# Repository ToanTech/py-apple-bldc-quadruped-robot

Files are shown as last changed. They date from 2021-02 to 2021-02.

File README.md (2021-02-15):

# py-apple-bldc-quadruped-robot
# 菠萝无刷四足机器人项目

## 1 简介  

  菠萝无刷四足机器人项目是由灯哥开源的，属于菠萝四足机器人项目的无刷分支。目前开源的机器人为  **菠萝无刷1代 测试版**。

  相应的文档和说明仍在不断撰写完善中，目前本 Github 的文件开源的内容主要为 **菠萝无刷1代 测试版** 的所有机械结构和软件程序；而机器人所采用的无刷电机FOC驱动开源资料和搭建方法开源在了另外的 Github上，见：  [灯哥开源FOC双路迷你无刷电机驱动](https://github.com/ToanTech/Deng-s-foc-controller)

  [菠萝无刷四足机器人项目总链接入口](https://github.com/ToanTech/py-apple-quadruped-robot)

## 2 项目文件说明

* src文件夹：存放测试本无刷四足机器人的 Pyboard 主控代码
* 3D model 文件夹：存放 菠萝无刷一代 三维模型
* BOM 文件夹：存放 菠萝无刷一代  机械+电控 BOM 表

## 3  项目原理及搭建教程

   本项目原理及搭建教程请见B站教学视频：

 [【教程】成本1K！从0教你DIY无刷四足机器人~灯哥无刷四足一代实验版开源啦！！！](https://www.bilibili.com/video/BV1kV411i76z/)

  DIY过程中由任何问题，欢迎加入QQ群聊交流：

  **开源无刷四足机器人交流群：1005923565**

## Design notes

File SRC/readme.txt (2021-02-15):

使用说明

1. Pyboard 测试程序放在基于 STM32 F4 的 Pyboard 内存之中
2. 灯哥开源FOC无刷驱动 程序 烧录进 灯哥开源无刷驱动版的 ESP32主控之中

前期文档未完善阶段，有问题欢迎加QQ群咨询：1005923565

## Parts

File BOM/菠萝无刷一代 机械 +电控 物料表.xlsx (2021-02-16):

部分名称 | 物料名称 | 物料规格 | 数量 | 注意
机械-单腿 | 螺丝 | M3*10 | 20 | 此为单腿数量，四条腿数量需x4
机械-单腿 | 螺丝 | M3*15 | 20 | 此为单腿数量，四条腿数量需x5
机械-单腿 | 螺丝 | M3*20 | 20 | 此为单腿数量，四条腿数量需x6
机械-单腿 | 轴承 | 6701ZZ | 2 | 此为单腿数量，四条腿数量需x7
机械-单腿 | 轴承 | 6704ZZ | 2 | 此为单腿数量，四条腿数量需x8
机械-单腿 | 防松螺母 | M3 | 10 | 此为单腿数量，四条腿数量需x9
机械-单腿 | 自行车车轮胶皮（足底防滑） | 根据实际需要 | 根据实际需要 | 此为单腿数量，四条腿数量需x10
机械-单腿 | 云台无刷电机 | 4008 150T（或类似参数电机） | 2 | 此为单腿数量，四条腿数量需x11
机械-单腿 | 同步带 | HTD-3M 318 6MM | 2 | 此为单腿数量，四条腿数量需x12
机械-身体 | 螺丝 | 3M*35 | 16
电控 | 电池 | 4S 16.8V电池 | 1
电控 | PyBoard | 基于STM32F4 的Pyboard | 1
电控 | 灯哥开源FOC无刷驱动板 | 见灯哥开源无刷驱动器GitHUB | 4
电控 | 杜邦线 |  | 若干

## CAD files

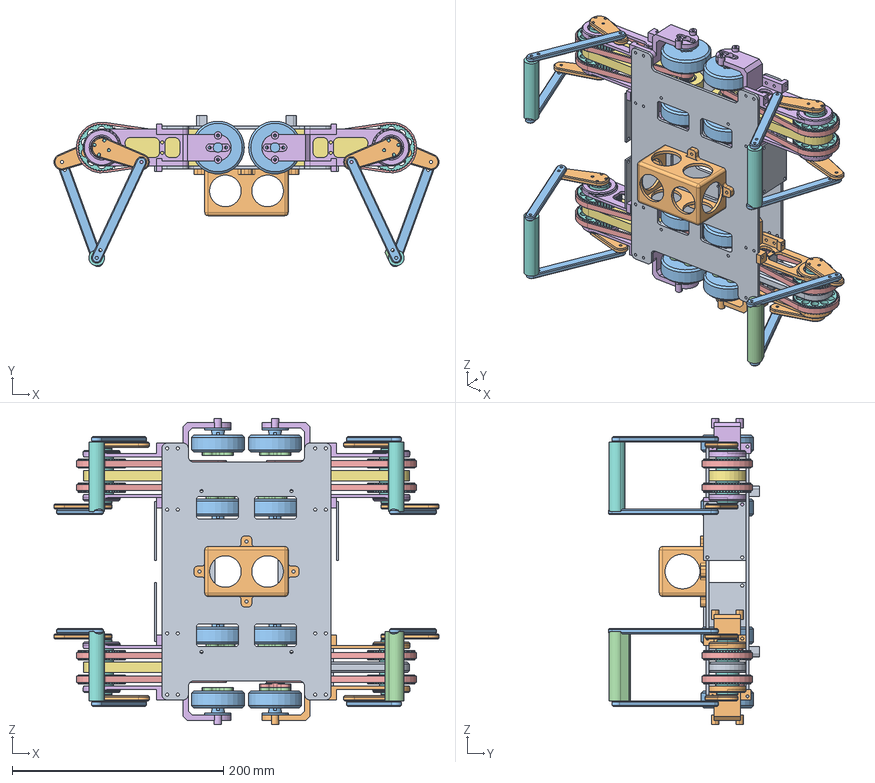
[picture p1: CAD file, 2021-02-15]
3D model/Py-apple BLDC quadruped robot V1.0.stp
364.1 x 143.2 x 289.8 mm
BODY_BOARD_V2 x 2
MOTOR_BINDER_V2 x 2
4008-MOTOR x 2
PULLEY_BRACKET x 2
REV_2_SMALL_PULLEY_LONG_PRINT x 2
OUTER_BEARING_6704-ZZ x 4
INNER_BEARING_6701-ZZ x 2
SDP_A_6A53M048NF0908_1 x 2
BACKGAP
TEST_N_GAN1 x 2
TEST_N_GAN_6 x 2
FOOT_FOOT
HTD210_3M_V2 x 2
MOTOR_BINDER_V2_MIR x 4
4008-MOTOR_MIR x 4
PULLEY_BRACKET_MIR x 4
OUTER_BEARING_6704-ZZ_MIR x 8
INNER_BEARING_6701-ZZ_MIR x 4
SDP_A_6A53M048NF0908_1_MIR x 4
BACKGAP_MIR x 2
TEST_N_GAN1_MIR x 4
TEST_N_GAN_6_MIR x 4
FOOT_FOOT_MIR x 2
HTD210_3M_V2_MIR x 4
BLDC_PCB_MIR x 2
MOTOR_BINDER_V2_MIR_MIR x 2
4008-MOTOR_MIR_MIR x 2
PULLEY_BRACKET_MIR_MIR x 2
OUTER_BEARING_6704-ZZ_MIR_MIR x 4
INNER_BEARING_6701-ZZ_MIR_MIR x 2
SDP_A_6A53M048NF0908_1_MIR_MIR x 2
BACKGAP_MIR_MIR
TEST_N_GAN1_MIR_MIR x 2
TEST_N_GAN_6_MIR_MIR x 2
FOOT_FOOT_MIR_MIR
HTD210_3M_V2_MIR_MIR x 2
BLDC_PCB_MIR_MIR
BATTERY_BIND_GAP

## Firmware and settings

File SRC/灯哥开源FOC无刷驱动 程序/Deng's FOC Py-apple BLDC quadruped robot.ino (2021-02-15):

/**
Copyright Deng（灯哥） (ream_d@yeah.net)  Py-apple dog project
Github:https:#github.com/ToanTech/py-apple-quadruped-robot
Licensed under the Apache License, Version 2.0 (the "License")
you may not use this file except in compliance with the License.
You may obtain a copy of the License at:http:#www.apache.org/licenses/LICENSE-2.0
 */
#include <SimpleFOC.h>
double init_p_sensor=0;
double init_p_sensor1=0;
int commaPosition;                //存储还没有分离出来的字符串 
double motor1_angle,motor2_angle;

MagneticSensorI2C sensor = MagneticSensorI2C(AS5600_I2C);
MagneticSensorI2C sensor1 = MagneticSensorI2C(AS5600_I2C);
TwoWire I2Cone = TwoWire(0);
TwoWire I2Ctwo = TwoWire(1);

// Motor instance
BLDCMotor motor = BLDCMotor(7);
BLDCDriver3PWM driver = BLDCDriver3PWM(32, 33, 25, 22);

BLDCMotor motor1 = BLDCMotor(7);
BLDCDriver3PWM driver1 = BLDCDriver3PWM(26, 27, 14, 12);

//HardwareSerial Serial2(2);
//定义 TROT 步态变量
void setup() {
  I2Cone.begin(18, 5, 400000); 
  I2Ctwo.begin(19, 23, 400000);
  sensor.init(&I2Cone);
  sensor1.init(&I2Ctwo);
  // link the motor to the sensor
  motor.linkSensor(&sensor);
  motor1.linkSensor(&sensor1);

  // driver config
  // power supply voltage [V]
  driver.voltage_power_supply = 16.8;
  driver.init();

  driver1.voltage_power_supply = 16.8;
  driver1.init();
  // link the motor and the driver
  motor.linkDriver(&driver);
  motor1.linkDriver(&driver1);
  
  // choose FOC modulation (optional)
  motor.foc_modulation = FOCModulationType::SpaceVectorPWM;
  motor1.foc_modulation = FOCModulationType::SpaceVectorPWM;
  // set motion control loop to be used
  motor.controller = ControlType::angle;
  motor1.controller = ControlType::angle;

  // contoller configuration 
  // default parameters in defaults.h

  // velocity PI controller parameters
  motor.PID_velocity.P = 0.2;
  motor1.PID_velocity.P = 0.2;
  motor.PID_velocity.I = 20;
  motor1.PID_velocity.I = 20;
  // maximal voltage to be set to the motor
  motor.voltage_limit = 16.8;
  motor1.voltage_limit = 16.8;
  
  // velocity low pass filtering time constant
  // the lower the less filtered
  motor.LPF_velocity.Tf = 0.01;
  motor1.LPF_velocity.Tf = 0.01;

  // angle P controller 
  motor.P_angle.P = 20;
  motor1.P_angle.P = 20;
  // maximal velocity of the position control
  motor.velocity_limit = 40;
  motor1.velocity_limit = 40;

  // use monitoring with serial 
  Serial.begin(115200);
  Serial2.begin(921600);
  // comment out if not needed
  motor.useMonitoring(Serial);
  motor1.useMonitoring(Serial);
  //记录无刷初始位置

  
  // initialize motor
  motor.init();
  motor1.init();
  // align sensor and start FOC
  motor.initFOC();
  motor1.initFOC();


  Serial.println("Motor ready.");
  init_p_sensor=sensor.getAngle();
  init_p_sensor1=sensor1.getAngle();
  Serial.println(init_p_sensor);
  Serial.println(init_p_sensor1);
  _delay(1000);
  
}

String serialReceiveUserCommand() {
  
  // a string to hold incoming data
  static String received_chars;
  
  String command = "";

  while (Serial2.available()) {
    // get the new byte:
    char inChar = (char)Serial2.read();
    // add it to the string buffer:
    received_chars += inChar;

    // end of user input
    if (inChar == '\n') {
      
      // execute the user command
      command = received_chars;

      //根据逗号分离两组字符串
      //想象中双足轮通讯数据格式:高度,指令   指令格式：英文+值
      commaPosition = command.indexOf(',');//检测字符串中的逗号
      if(commaPosition != -1)//如果有逗号存在就向下执行
      {
          motor1_angle = command.substring(0,commaPosition).toDouble();            //一号电机角度
          motor2_angle = command.substring(commaPosition+1, command.length()).toDouble();//打印字符串，从当前位置+1开始
          //Serial.println(motor1_angle);
          //Serial.println(motor2_angle);
      }
      // reset the command buffer 
      received_chars = "";
    }
  }
  return command;
}


void loop() {

  // main FOC algorithm function
  // the faster you run this function the better
  // Arduino UNO loop  ~1kHz
  // Bluepill loop ~10kHz 
  motor.loopFOC();
  motor1.loopFOC();

  // Motion control function
  // velocity, position or voltage (defined in motor.controller)
  // this function can be run at much lower frequency than loopFOC() function
  // You can also use motor.move() and set the motor.target in the code

  //Serial.println(sita1_1);
  //Serial.println(sita2_1);
  motor.move(init_p_sensor+motor1_angle);
  motor1.move(init_p_sensor1+motor2_angle); 
  //Serial2.println("sssd"); 
  serialReceiveUserCommand();

}

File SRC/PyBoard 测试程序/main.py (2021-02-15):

#Copyright Deng（灯哥） (ream_d@yeah.net)  Py-apple dog project
#Github:https:#github.com/ToanTech/py-apple-quadruped-robot
#Licensed under the Apache License, Version 2.0 (the "License")
#you may not use this file except in compliance with the License.
#You may obtain a copy of the License at:http:#www.apache.org/licenses/LICENSE-2.0

from math import sin,cos,pi,sqrt,asin,acos
from pyb import UART
u1=UART(2,921600)   #Tx:x3 Rx：x4
u2=UART(1,921600)   #Tx:x9 Rx：x10
u3=UART(3,921600)   #Tx:y9 Rx：y10
u4=UART(4,921600)   #Tx:x1 Rx：x2

t=0
pi = 3.1415926;height=-100
x1=0;x2=0;x3=0;x4=0;Y1=0;y2=0;y3=0;y4=0
r1=1;r2=1;r3=1;r4=1
faai=0.5;Ts=1
xf=40;xs=-40;h=45
sita1_1=0;sita2_1=0
l1=35;l2=80


def trot():
    global Y1,y2,y3,y4
    global x1,x2,x3,x4
    if t<=Ts*faai:
        sigma=2*pi*t/(faai*Ts)
        zep=h*(1-cos(sigma))/2
        xep_b=(xf-xs)*((sigma-sin(sigma))/(2*pi))+xs
        xep_z=(xs-xf)*((sigma-sin(sigma))/(2*pi))+xf
        #输出y
        Y1=zep+height
        y2=0+height
        y3=zep+height
        y4=0+height
        #输出x
        x1=-xep_z*r1
        x2=-xep_b*r2
        x3=-xep_z*r3
        x4=-xep_b*r4
    elif t>Ts*faai and t<=Ts:
        sigma=2*pi*(t-Ts*faai)/(faai*Ts)
        zep=h*(1-cos(sigma))/2
        xep_b=(xf-xs)*((sigma-sin(sigma))/(2*pi))+xs
        xep_z=(xs-xf)*((sigma-sin(sigma))/(2*pi))+xf
        #输出y
        Y1=0+height
        y2=zep+height
        y3=0+height
        y4=zep+height
        #输出x
        x1=-xep_b*r1
        x2=-xep_z*r2
        x3=-xep_b*r3
        x4=-xep_z*r4

def ik():
    global sita1_1,sita2_1,Y1
    global sita1_2,sita2_2,y2
    global sita1_3,sita2_3,y3
    global sita1_4,sita2_4,y4
    #腿1
    Y1=-Y1
    L1=sqrt(x1*x1+Y1*Y1)
    psai1=asin(x1/L1)
    fai1=acos((L1*L1+l1*l1-l2*l2)/(2*l1*L1))
    sita1_1=round((fai1-psai1)*3,2)
    sita2_1=round((fai1+psai1)*3,2)
    #腿2
    y2=-y2
    L2=sqrt(x2*x2+y2*y2)
    psai2=asin(x2/L2)
    fai2=acos((L2*L2+l1*l1-l2*l2)/(2*l1*L2))
    sita1_2=round((fai2-psai2)*3,2)
    sita2_2=round((fai2+psai2)*3,2)
    #腿3
    y3=-y3
    L3=sqrt(x3*x3+y3*y3)
    psai3=asin(x3/L3)
    fai3=acos((L3*L3+l1*l1-l2*l2)/(2*l1*L3))
    sita1_3=round((fai3-psai3)*3,2)
    sita2_3=round((fai3+psai3)*3,2)
    #腿4
    y4=-y4
    L4=sqrt(x4*x4+y4*y4)
    psai4=asin(x4/L4)
    fai4=acos((L4*L4+l1*l1-l2*l2)/(2*l1*L4))
    sita1_4=round((fai4-psai4)*3,2)
    sita2_4=round((fai4+psai4)*3,2)
    
while True:
    t=t+0.01
    if t>=Ts:
        t=0
    trot()
    ik()
    u1.write(str(-sita1_1)+","+str(sita2_1)+'\n')
    u2.write(str(sita1_2)+","+str(-sita2_2)+'\n')
    u3.write(str(-sita1_4)+","+str(sita2_4)+'\n')
    u4.write(str(-sita1_3)+","+str(sita2_3)+'\n')
    #print("sita1_1",sita1_1)
    #print("sita2_1",sita2_1)
    print(str(sita1_2)+","+str(sita2_2))

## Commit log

2021-02-15 Add readme
    [菠萝无刷一代 机械 +电控 物料表.xlsx]
2021-02-15 Update Py apple BLDC quadruped V1.0
    [Py-apple BLDC quadruped robot V1.0.stp]
